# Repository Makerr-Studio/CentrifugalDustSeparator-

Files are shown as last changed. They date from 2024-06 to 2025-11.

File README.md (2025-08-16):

# CentrifugalDustSeparator
Centrifugal Dust Separator - MK2 - 3D Files for printing (Beta release)<br>
Support me on: https://www.patreon.com/CapturingDust

Tube suppliers may vary based on your geographic location, and so do the tube dimensions.<br>
Files are adjusted accordingly, see README files in the spesific build versions for suppliers info:<br>
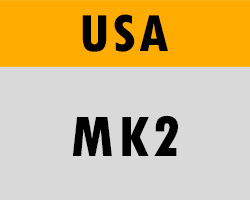
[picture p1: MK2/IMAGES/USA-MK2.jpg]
 
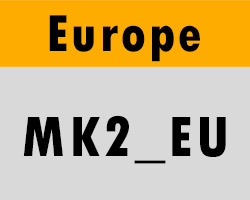
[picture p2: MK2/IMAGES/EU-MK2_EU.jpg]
 
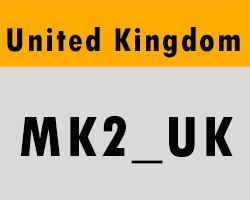
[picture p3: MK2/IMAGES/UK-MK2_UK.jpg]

<br>*note: First print the scaling ring to check your tube dimensions. See: https://www.youtube.com/shorts/JZXLTLeB2oE
<br>**note: For parts that are not listed in the subfolders (such as the Y-pieces) see the normal MK2 version.<br>

All parts are designed to print on bambulab build volume(WxDxH) 256 x 256 x 256 mm³.<br>
Only the Y-pieces are not compatable with the Prusa build plate.
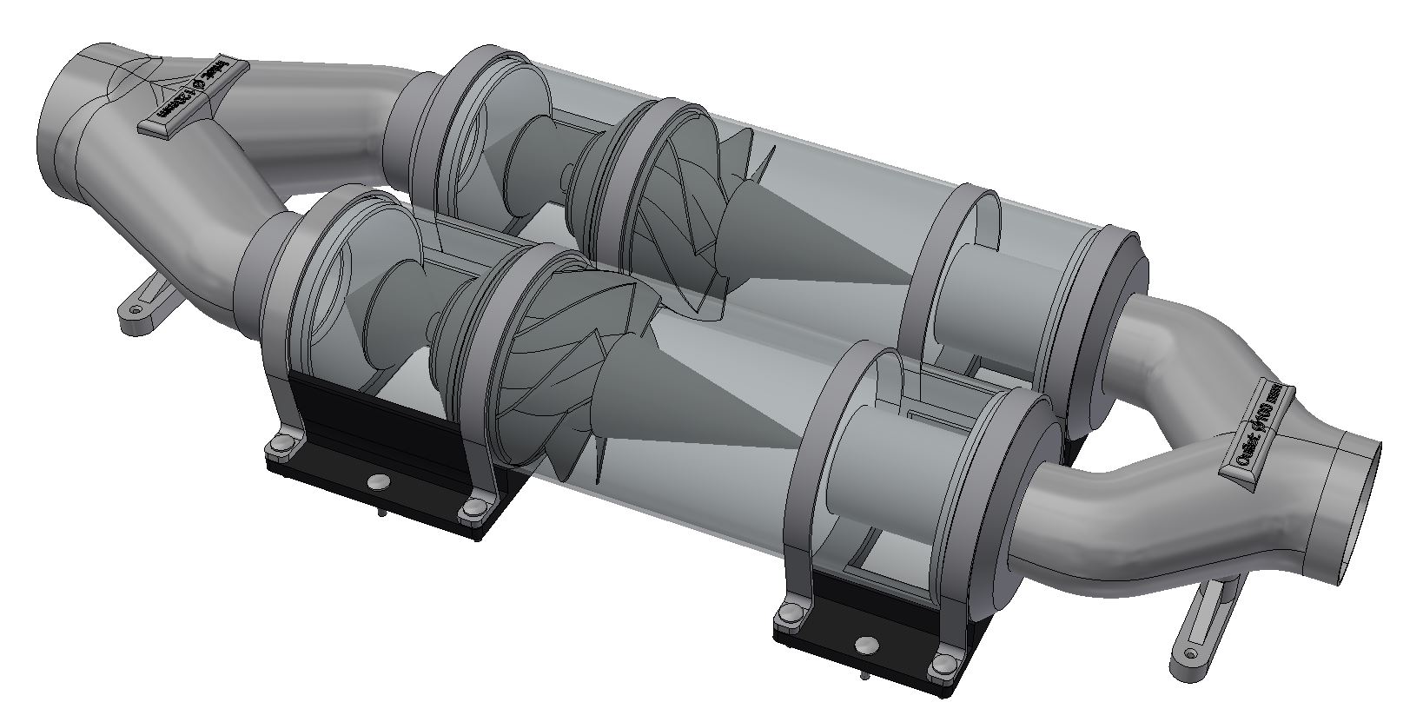
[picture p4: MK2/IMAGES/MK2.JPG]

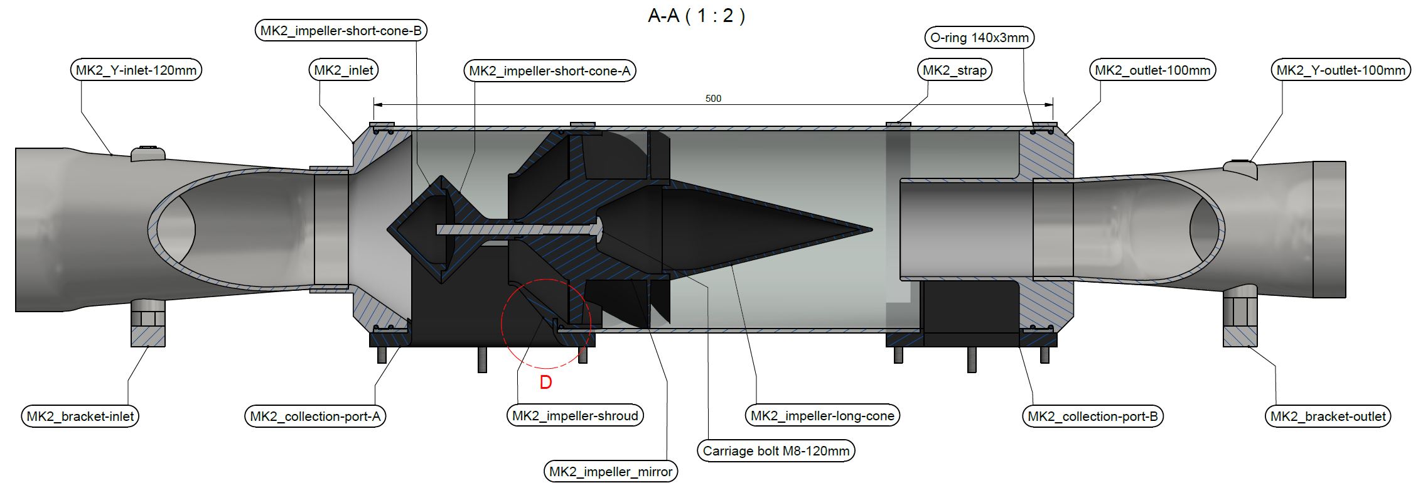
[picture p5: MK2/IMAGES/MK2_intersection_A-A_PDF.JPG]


<h2>YouTube: @CapturingDust</h2>
For the test video see:

https://www.youtube.com/watch?v=ENybYVAr11Q&t=1102s

Part 1 of the build video is available on Youtube: https://www.youtube.com/watch?v=bCNDPIjRccw

Part 2 of the build video is available on Youtube:
https://www.youtube.com/watch?v=j7K9fEa8Re8

<h2>Parts/Supplies:</h2>
The MK2 base version is designed for 6" Clear PVC  = https://www.amazon.com/dp/B09NJLNW58?psc=1&ref=ppx_yo2ov_dt_b_product_details

<br>EU alternative Acrylic tube 150x3mm (real size 151x3.5mm)= https://www.kunststofforte.nl/product/transparante-acrylaat-buizen-xt/<br>
UK alternative Acrylic tube 150x3mm (real size 150.05x3.1mm)= https://plasticonline.co.uk/150mm-diameter-clear-acrylic-tube.html

O-ring MK2     = https://www.kramp.com/shop-de/de/p/o-ring-140-x-3--OR1403P001
<br>O-Ring MK2_EU  = https://www.kramp.com/shop-de/de/p/o-ring-120-x-3--OR1203P001

Collection container        = Festool VAB-20/1 part nr. 204294 (204295 in my case because its a pack of 3).
<br>(For US: $79.60 set of 3 - Free shipping: https://www.hartvillehardware.com/product/sku-1337339/festool-dust-extractors-accessories)

Compresion tape: 50 mm x 30 m x 3mm version of this tape: https://bluedolphintapes.com/product/acoustic-tape/

3D printable Systainer T-Loc: https://www.printables.com/model/313989-systainer-t-loc

<h2>Original build</h2>
Inspired by Pilson Guitars build project<br>
Youtube: https://www.youtube.com/watch?v=R4R9GfCQrW4&<br>
Github: https://github.com/pilsonguitars/centrifugalDustSeparator

<h2>Changelog:</h2><br>
16-08-2025: 200mm single tube Centrifugal dust Separator STEP-files added. Including third stage integration. Used Acrylic tube 200x3mm from: https://www.kunststofforte.nl/product/transparante-acrylaat-buizen-xt/ 
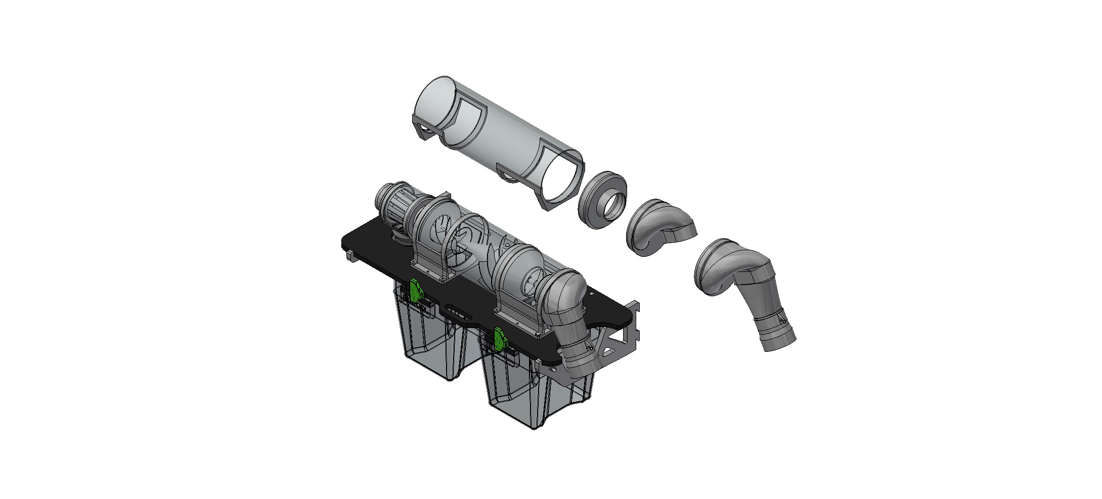
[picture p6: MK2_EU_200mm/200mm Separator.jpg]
<br>
15-01-2025: STEP-files of Y-piece, bracked and inlet added for 100mm tube to MK2 and MK2_EU. <br>
06-10-2024: Prusa printable Y-pieces added to folder <a target="_blank" rel="noopener noreferrer" href="MK2/STEP/">MK2/STEP</a><br>
29-09-2024: Changed the README file to better explain the differend design folder.<br>
28-09-2024: I did find out that a normal nut won't lock the impeller assembly for the long run. PLA will shrink/compress over time, and loosens the nut. Use a spring washer & lock nut instead!<br>
14-09-2024: Added the REV2 files of the Y-pieces + brackeds. They need less material to print now by removing the needs for support. Thx @philreindl for the tip!<br>
11-09-2024: In the folder <a target="_blank" rel="noopener noreferrer" href="MK2_EU/">MK2_EU</a> I added the Shaper files (.svg and also the .DXF's) and the Fusion archive files (.f3d) of the baseplate and cleat.<br>
08-09-2024: Parts for the French Cleats added. Fusion file is in the making. Type of compresion tape added.<br>
05-09-2024: Parts for the T-Loc added. Note: I did not print the latch and latch cover (these are just the 3D STEP files I used for the design, feel free to try to 3D print them)<br>
24-08-2024: MK2_EU Inlet and outlet parts adjusted for a better O-ring seal/fit for the 120x3mm O-rings.<br>
19-08-2024: Added 120x3mm O-rings i switced to while building the EU version. Still need to change the parts for a better fit. Will make testprints for this in the next weeks.<br>
10-08-2024: Added BAMBU LAB and OrcaSlicer files to MK2_UK.<br>
07-08-2024: <a target="_blank" rel="noopener noreferrer" href="MK2_UK/">MK2_UK</a> Step Files added for UK version Tube. Not printed of tested yet. <br>
07-08-2024: <a target="_blank" rel="noopener noreferrer" href="MK2_EU/">MK2_EU</a> files added for EU alternative. Not tested jet. <br>
02-08-2024: OrcaSlicer file from mirrored impeller added.<br>
01-08-2024: All .3fm files are available now. Also added all the .stl-files.<br>
29-07-2024: To solve issues with print imperfections on the mirrored impeller; Use the open-source OrcaSlicer and set the wall loop direction to clockwise. Thx @Mik3503 for the tip!
(*Go to the <a target="_blank" rel="noopener noreferrer" href="[MK2/STEP/](https://github.com/SoftFever/OrcaSlicer/releases)">GitHub</a> page, scroll down to the assets section and download the latest release compatible with your operating system, and then install it)<br>
21-07-2024: Folder BAMBU LAB added with the .3mf files for Bambu Lab. Added the impeller and impeller-mirror and fixed the Non-manifold edges error. (Working on the other .3fm files to add)

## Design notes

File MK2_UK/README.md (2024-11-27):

Files adjusted for UK tube: https://plasticonline.co.uk/150mm-diameter-clear-acrylic-tube.html
<br>Print the mirrored impeller with the OrcaSlicer file clockwise for clean print results.

I adjusted the MK2 files to the UK tube dimensions:

    Wall thickness: 3.1mm
    OD: 150.05mm
    ID: 144.16mm

*had to scale down MK2_UK_impeller-shroud.3mf (along with the impeller) to 99.9 as at 100% it was just too snug to push further down the tube past the opening. Check your tube dimensions always with the scaling ring.

Github member <a target="_blank" rel="noopener noreferrer" href="https://github.com/3dtrix">3dtrix</a> from Germany purchased his tubes from this online shop (Original Plexiglas manufacture):
<br>150mm / 3mm
<br>https://www.plexiglas-shop.com/de/produkte/ro0a070gt.html
<br>They ship to EU incl. UK<br><br>

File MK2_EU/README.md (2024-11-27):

Centrifugal Dust Separator - MK2_EU - 3D Files for printing (Beta release)<br>
Support me on: https://www.patreon.com/CapturingDust

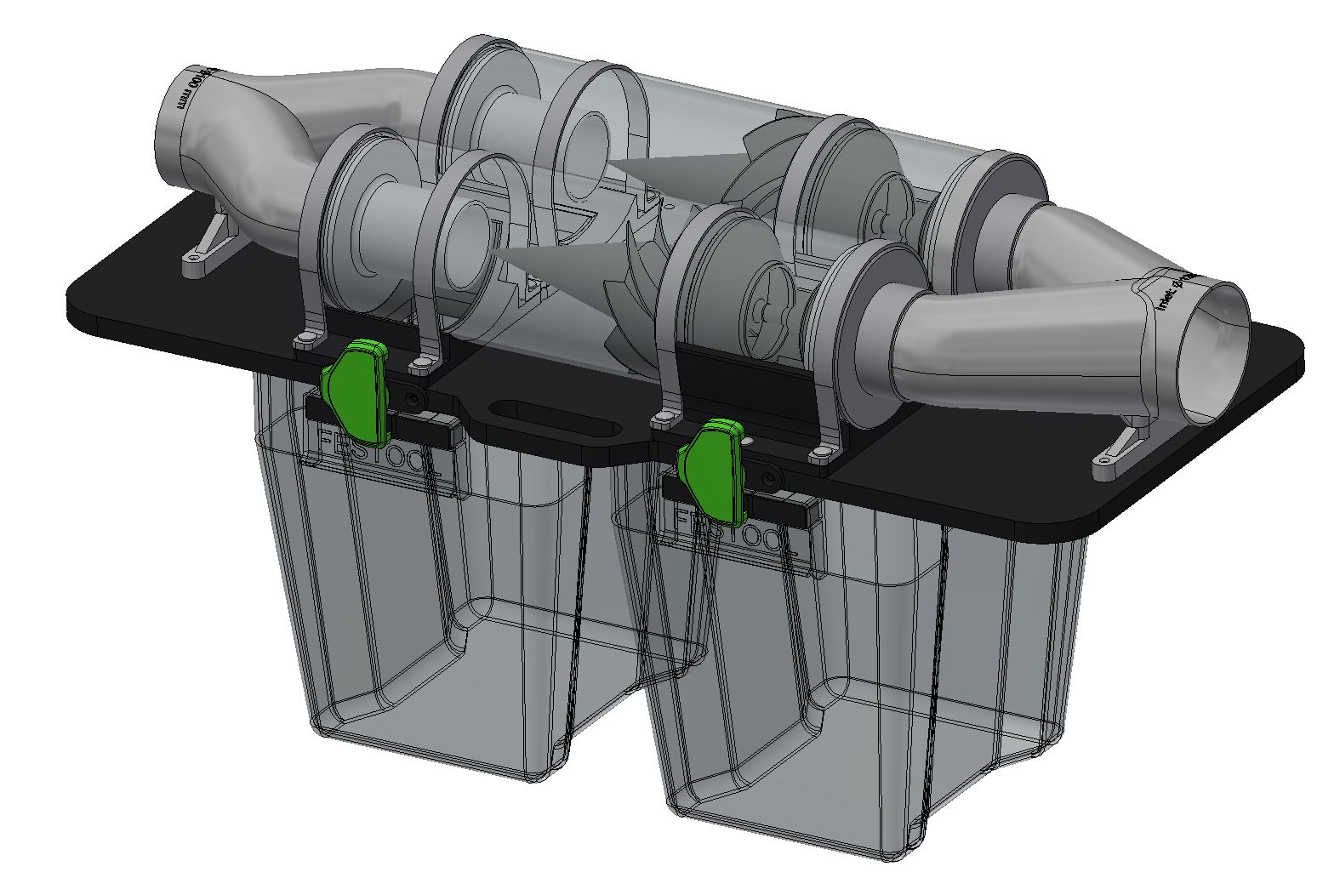
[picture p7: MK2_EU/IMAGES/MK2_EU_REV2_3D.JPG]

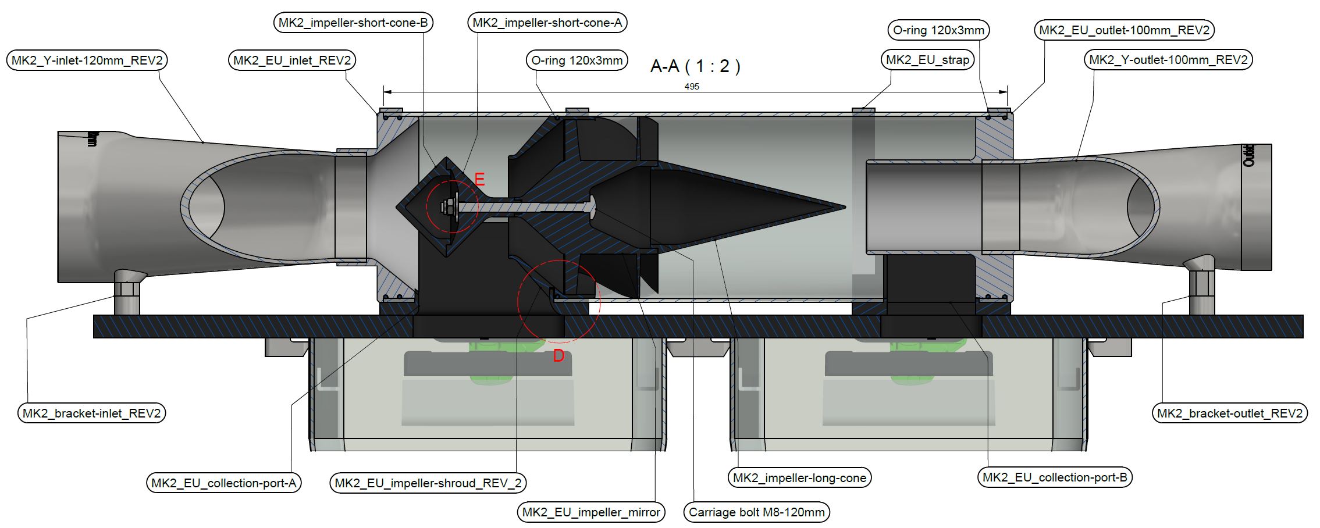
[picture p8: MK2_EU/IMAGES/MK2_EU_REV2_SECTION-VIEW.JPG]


Files adjusted for EU 150x3mm tube: https://www.kunststofforte.nl/product/transparante-acrylaat-buizen-xt/
Print the mirrored impeller with the OrcaSlicer file clockwise for clean print results.

120x3mm O-Ring EU = https://www.techniekwebshop.nl/o-ring-120-x-3-or1203p001-makkelijk-vervormbaar-precisie-o-ring-nitrilrubber-nbr-din-3771-70-amp-deg-sh-120-mm.html

I adjusted the MK2 files to the real life EU Kunststofforte tube dimensions I measured:

    Wall thickness: 3.5 mm
    OD: 151,375 mm
    ID: 144,375 mm

Patreon member purchased his tubes at a German seller on Amazon: https://www.amazon.com.be/dp/B0CBKV2Y2K
<br>    ID: 143,46 mm
<br>    EU Files printed at 99.4% scale (Check your tube dimensions always with the scaling ring.)

Github member <a target="_blank" rel="noopener noreferrer" href="https://github.com/3dtrix">3dtrix</a> from Germany purchased his tubes from this online shop (Original Plexiglas manufacture):
<br>150mm / 3mm
<br>https://www.plexiglas-shop.com/de/produkte/ro0a070gt.html
<br>They ship to EU incl. UK<br><br>

<h2>Latest versions</h2>
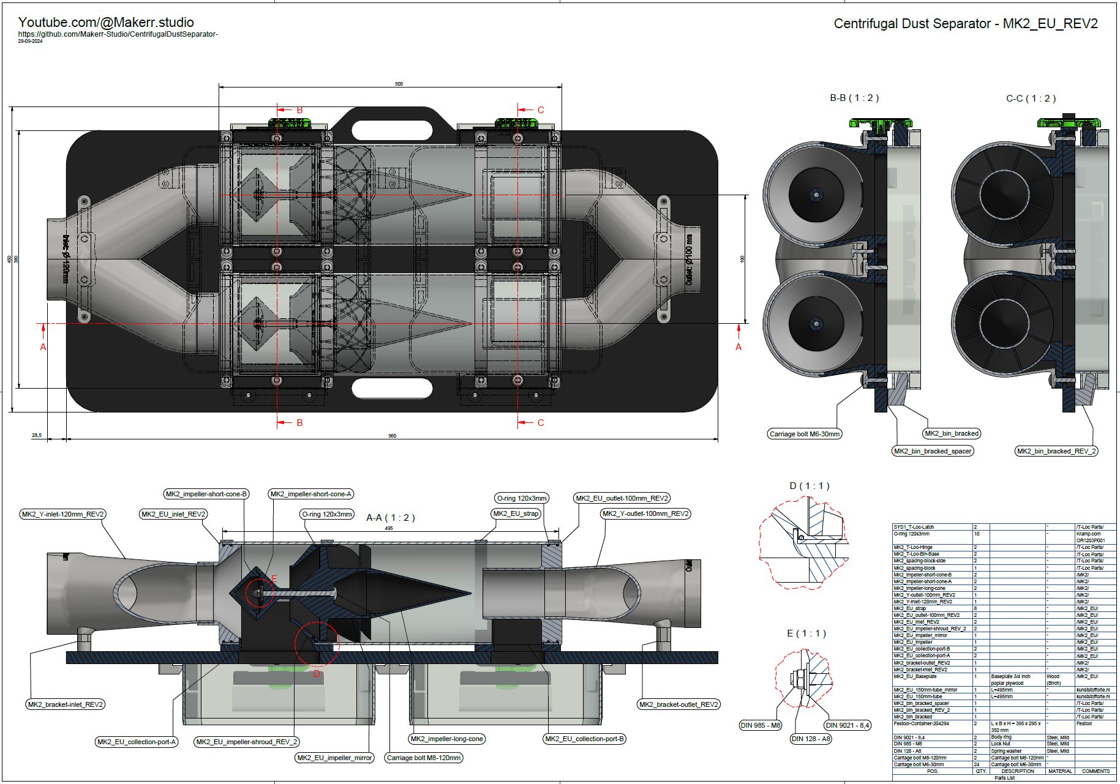
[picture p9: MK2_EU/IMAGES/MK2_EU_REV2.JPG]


<h2>Old versions</h2>
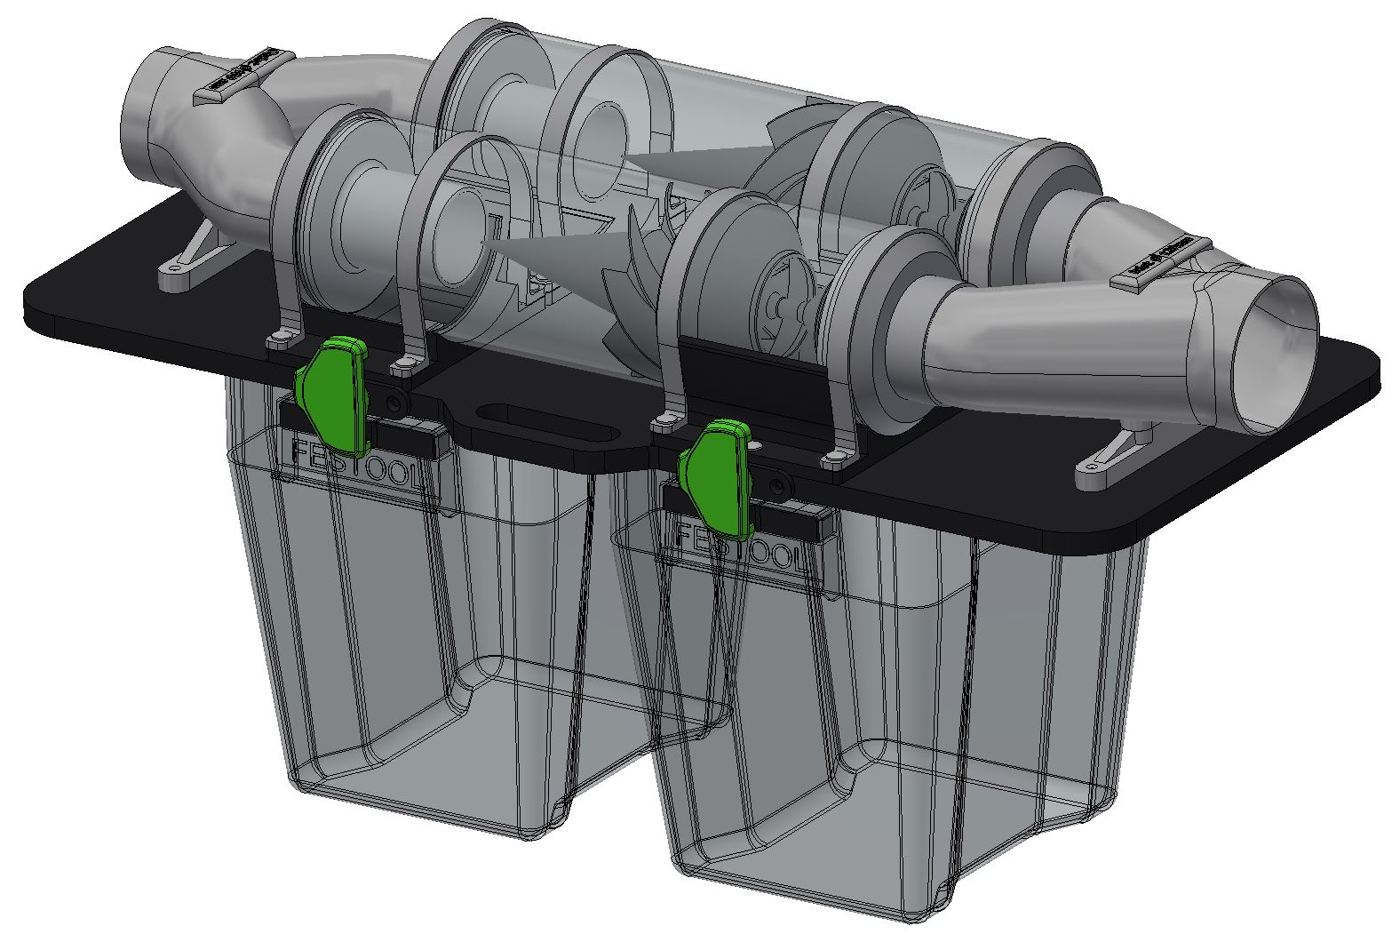
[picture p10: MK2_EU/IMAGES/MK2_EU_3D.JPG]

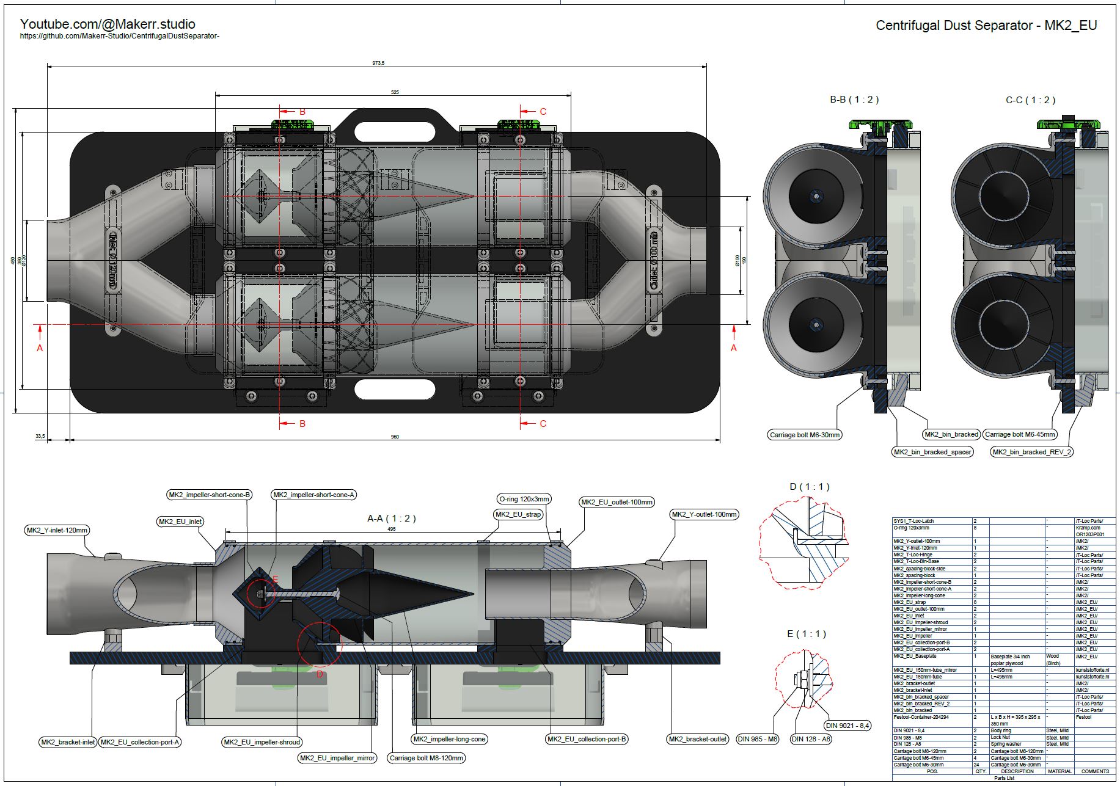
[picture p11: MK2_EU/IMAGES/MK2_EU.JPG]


<h2>Changelog:</h2><br>
29-09-2024: Completed the drawing files of MK2_EU_REV2. Added the STEP-files for the REV2 parts.<br>
24-08-2024: Inlet and outlet parts adjusted for a better O-ring seal/fit for the 120x3mm O-rings.<br>
19-08-2024: Added 120x3mm O-rings I switched to while building the EU version. Still need to change the parts for a better seal/fit. Will make testprints for this in the next week.

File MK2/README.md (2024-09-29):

The MK2 base version is designed for 6" Clear PVC  = https://www.amazon.com/dp/B09NJLNW58?psc=1&ref=ppx_yo2ov_dt_b_product_details<br>

Tube dimensions I measured:

    Wall thickness: 3,01 mm
    OD: 151,822 mm
    ID: 145,800 mm

Patreon member purchased his tubes at Woodcraft: 
<br>  https://www.woodcraft.com/products/woodriver-dust-connection-clear-pvc-tube-36-x-6 
<br>  Free Shipping with Code "PENCIL" $20 each
<br>Check your tube dimensions always with the scaling ring.

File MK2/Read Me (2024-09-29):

The MK2 base version is designed for 6" Clear PVC  = https://www.amazon.com/dp/B09NJLNW58?psc=1&ref=ppx_yo2ov_dt_b_product_details<br>

Tube dimensions I measured:

    Wall thickness: 3,01 mm
    OD: 151,822 mm
    ID: 145,800 mm

Patreon member purchased his tubes at Woodcraft: 
  https://www.woodcraft.com/products/woodriver-dust-connection-clear-pvc-tube-36-x-6 
  Free Shipping with Code "PENCIL" $20 each
  MK2 Files printed at 99.6% scale

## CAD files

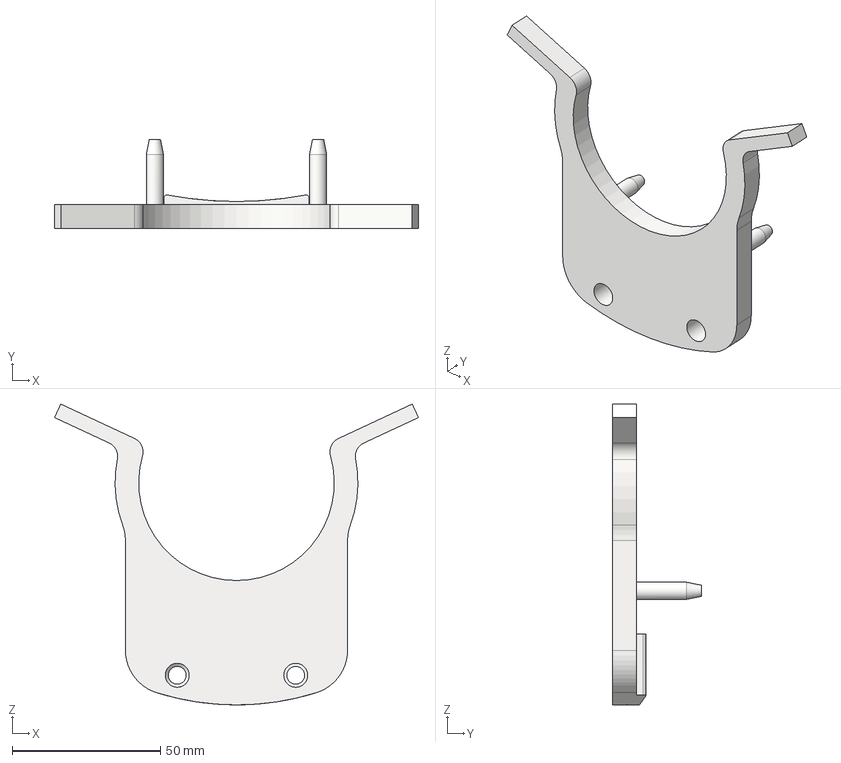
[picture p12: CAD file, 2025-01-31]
BT-100 Anemometer Jig/BT-100-JIG_Base.stp
122.9 x 30.0 x 101.6 mm

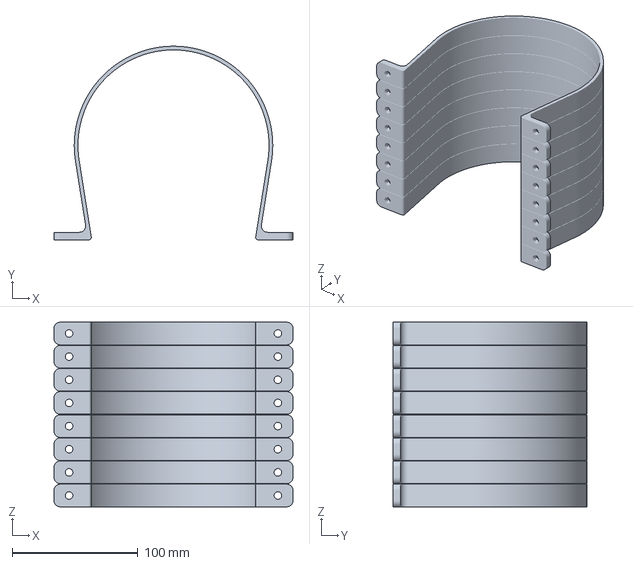
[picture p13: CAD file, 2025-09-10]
MK2/BAMBU LAB/MK2_strap_stacked.3mf
190.0 x 153.9 x 146.8 mm

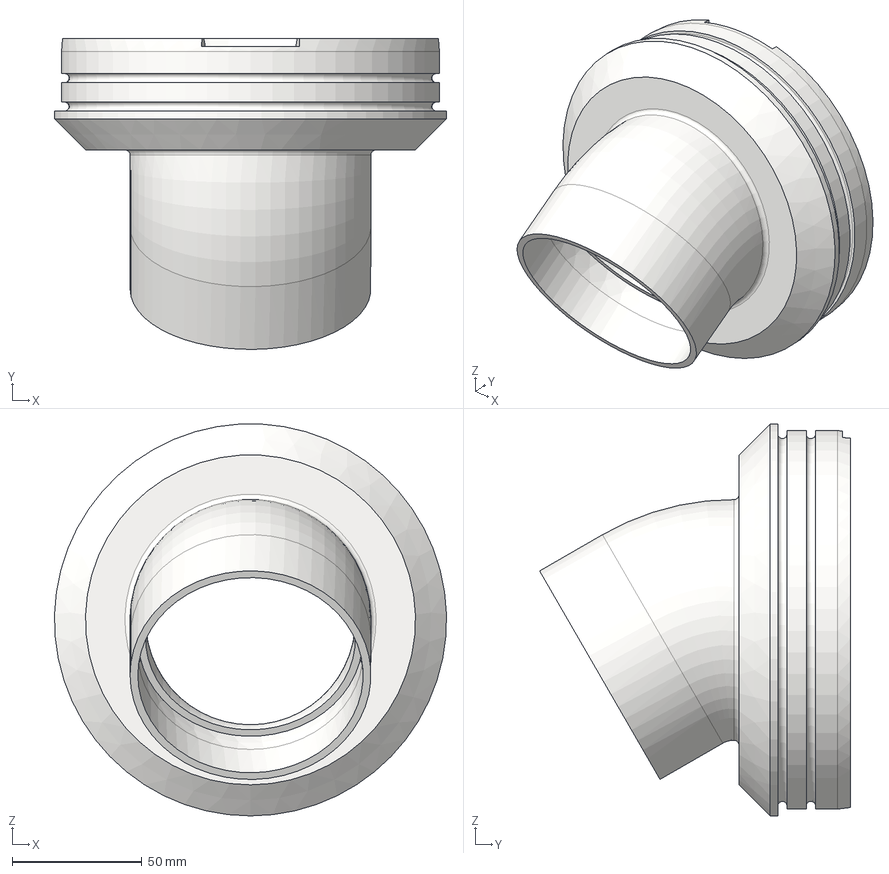
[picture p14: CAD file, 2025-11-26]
MK2/NOT TESTED - REQUESTED PARTS/MK2_inlet-30-degrees.stp
151.4 x 120.0 x 151.3 mm

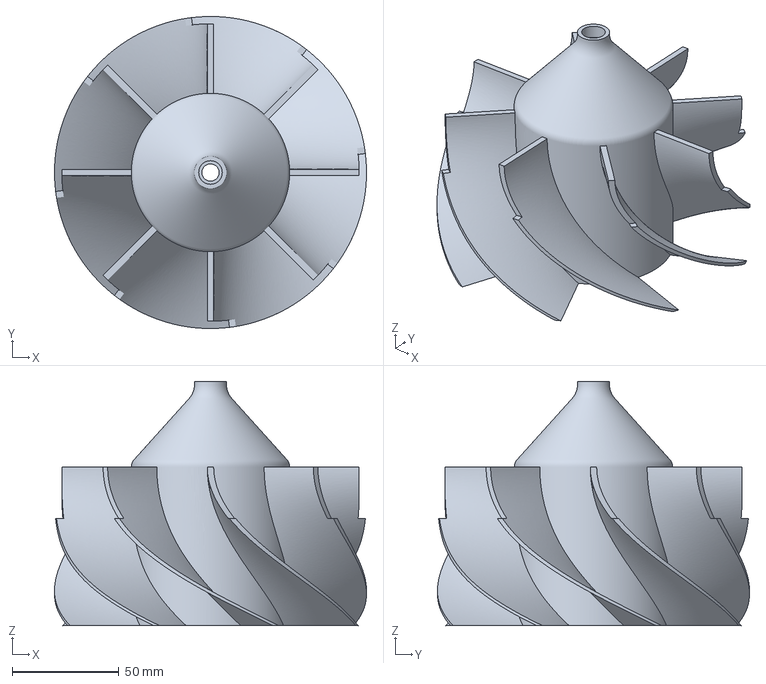
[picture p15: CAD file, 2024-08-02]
MK2/OrcaSlicer/MK2_impeller_mirror.3mf
145.8 x 145.8 x 114.2 mm

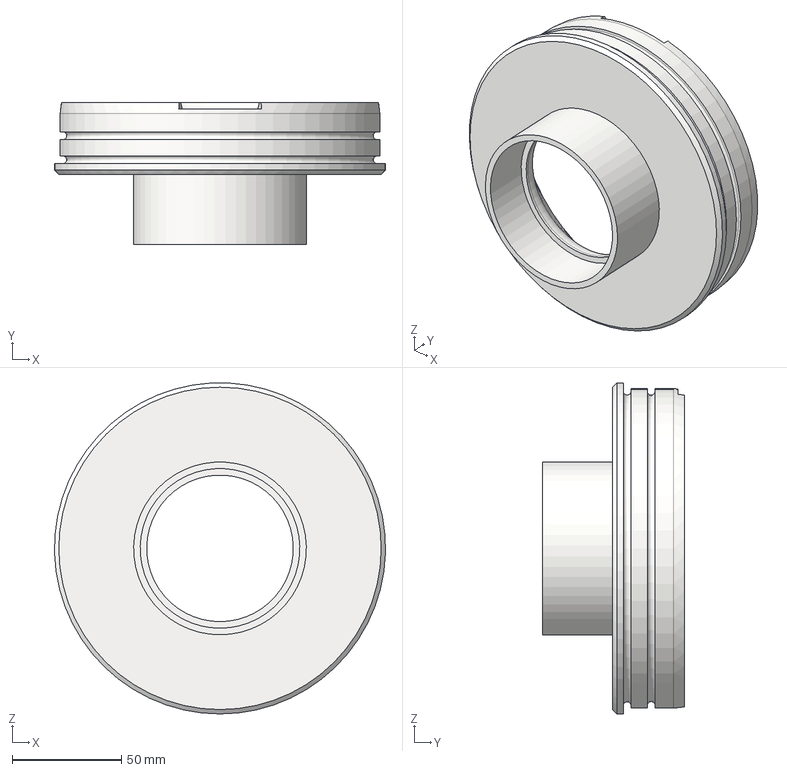
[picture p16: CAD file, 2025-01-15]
MK2/STEP/MK2_inlet_100mm_REV2.stp
151.4 x 65.0 x 151.3 mm

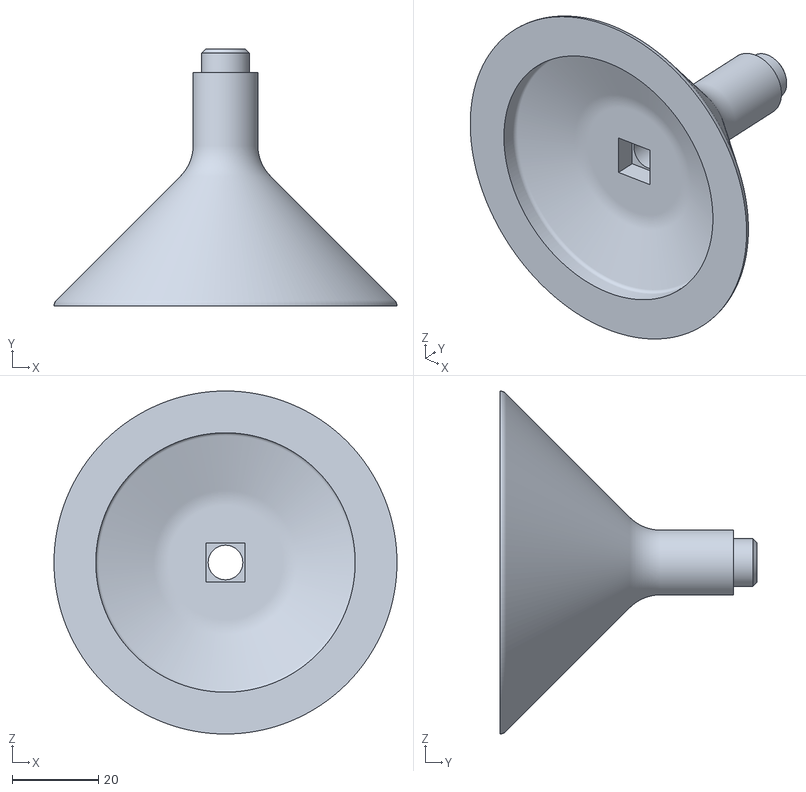
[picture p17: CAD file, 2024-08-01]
MK2/STL/MK2_impeller-short-cone-A.stl
79.3 x 59.5 x 79.3

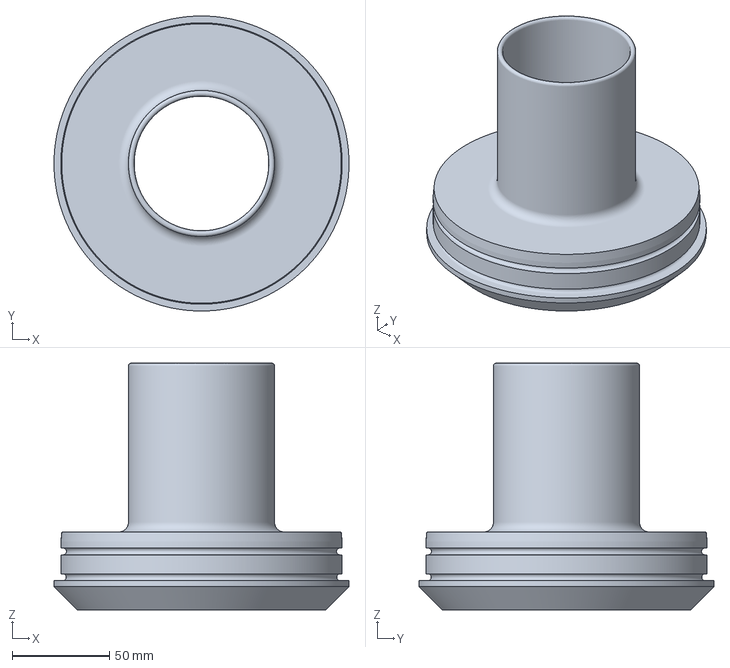
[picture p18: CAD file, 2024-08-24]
MK2_EU/BAMBU LAB/MK2_EU_outlet-100mm.3mf
151.4 x 151.4 x 126.6 mm

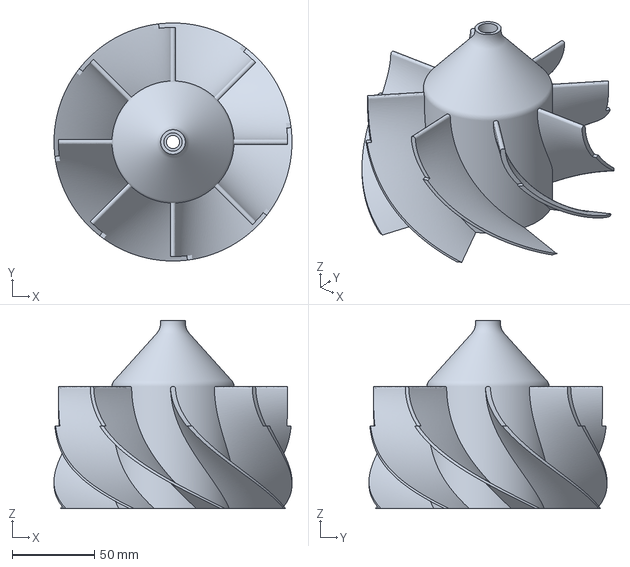
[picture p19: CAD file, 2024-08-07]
MK2_EU/OrcaSlicer/MK2_EU_impeller_mirror.3mf
144.4 x 144.4 x 114.2 mm

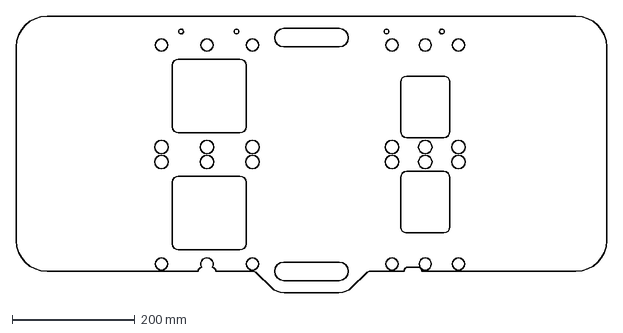
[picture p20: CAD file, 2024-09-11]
MK2_EU/Shaper/MK2_EU_baseplate.dxf
960.0 x 450.0 mm

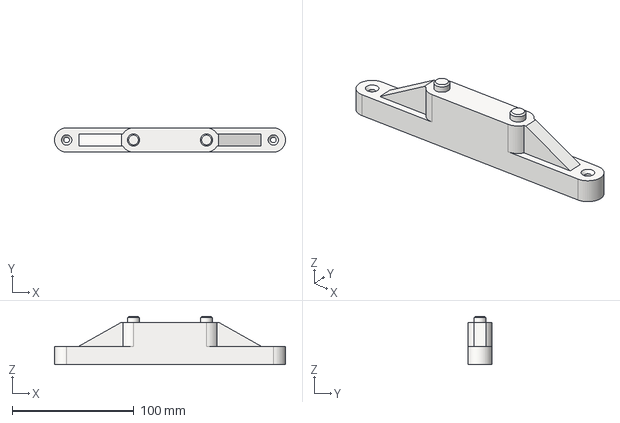
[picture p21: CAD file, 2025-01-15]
MK2_EU/STEP/MK2_EU_bracket-inlet-100mm.stp
190.0 x 20.0 x 39.5 mm

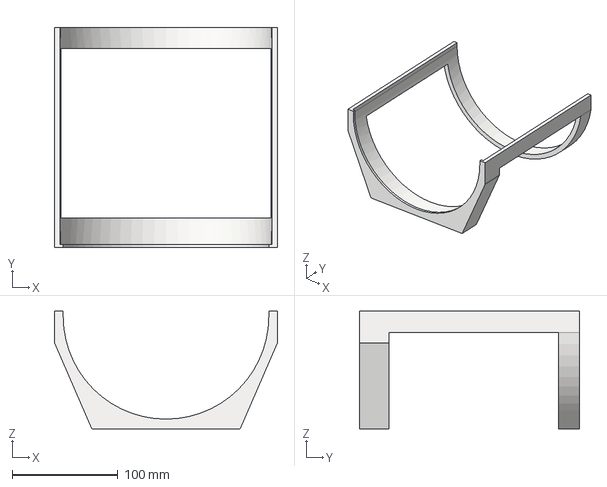
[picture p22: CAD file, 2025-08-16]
MK2_EU_200mm/MK2_EU_8inch_A-cutting-jig.stp
210.6 x 208.0 x 111.4 mm

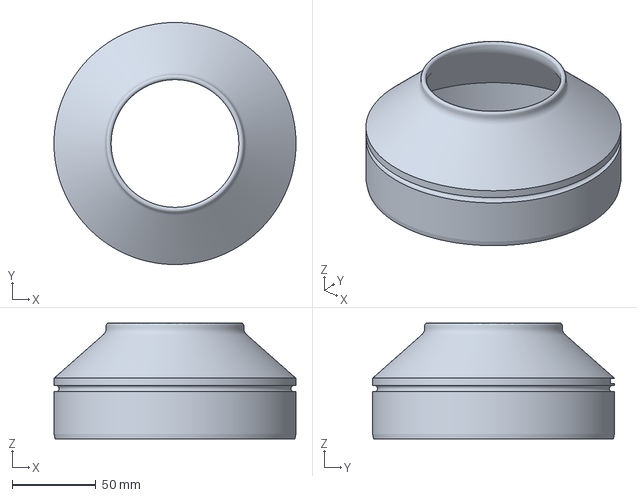
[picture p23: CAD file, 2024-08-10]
MK2_UK/BAMBU LAB/MK2_UK_impeller-shroud-o-ring.3mf
144.2 x 144.2 x 69.0 mm

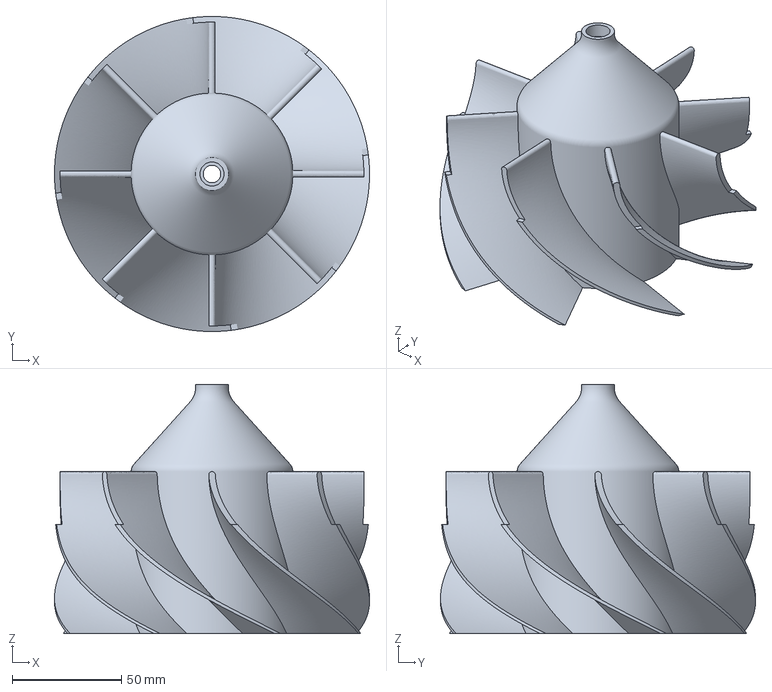
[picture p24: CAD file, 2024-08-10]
MK2_UK/OrcaSlicer/MK2_UK_impeller_mirror.3mf
144.1 x 144.1 x 114.2 mm

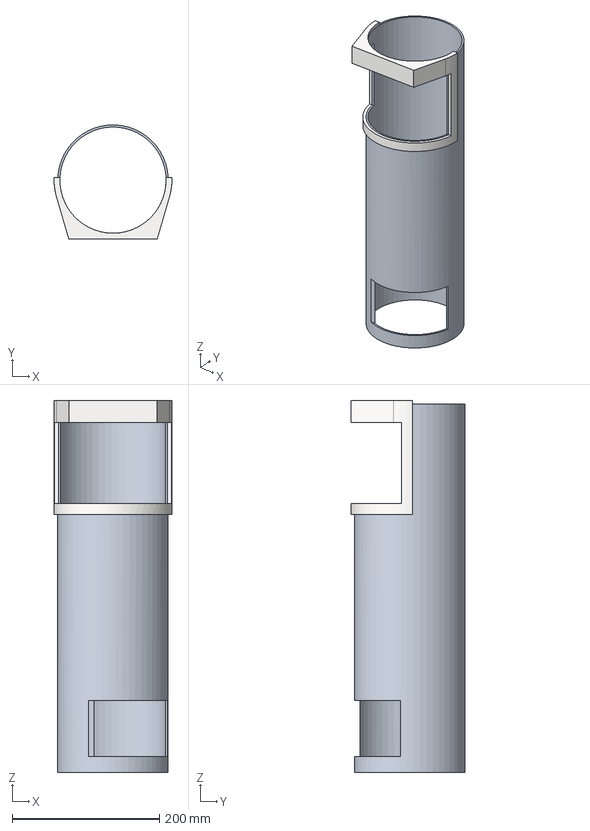
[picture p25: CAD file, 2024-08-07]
MK2_UK/STEP/MK2_UK_port-A-cutting-jig.stp
159.9 x 155.0 x 505.0 mm

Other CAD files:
T-Loc Parts/Festool-Container-204294.stp
BT-100 Anemometer Jig/BT-100-JIG_insert_100mm.stp
MK2/BAMBU LAB/MK2_bracket-outlet_REV2.3mf
MK2/NOT TESTED - REQUESTED PARTS/MK2_inlet-45-degrees.stp
BT-100 Anemometer Jig/BT-100-JIG.3mf
BT-100 Anemometer Jig/BT-100-JIG_insert_120mm.stp
MK2/BAMBU LAB/MK2_Y-outlet-100mm_REV2.3mf
MK2/BAMBU LAB/MK2_bracket-inlet.3mf
MK2/BAMBU LAB/MK2_bracket-inlet_REV2.3mf
MK2/BAMBU LAB/MK2_bracket-outlet.3mf
MK2/BAMBU LAB/MK2_collection-port-A.3mf
MK2/BAMBU LAB/MK2_collection-port-B.3mf
MK2/BAMBU LAB/MK2_impeller-mirror.3mf
MK2/BAMBU LAB/MK2_impeller-short-cone-A.3mf
MK2/BAMBU LAB/MK2_impeller-short-cone-B.3mf
MK2/BAMBU LAB/MK2_impeller-shroud.3mf
MK2/BAMBU LAB/MK2_impeller.3mf
MK2/BAMBU LAB/MK2_inlet.3mf
MK2/BAMBU LAB/MK2_outlet-100mm.3mf
MK2/BAMBU LAB/MK2_port-A-cutting-jig.3mf
MK2/BAMBU LAB/MK2_port-B-cutting-jig-mirror.3mf
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

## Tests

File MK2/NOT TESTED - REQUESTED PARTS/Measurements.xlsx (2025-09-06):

 | % | KG/h
A | 99.57 | 33.3214
A | 99.83 | 93.945
A | 99.86 | 100.975
A | 99.85 | 139.764
A | 99.77 | 253.573
A | 98.85 | 281.02
A | 98.23 | 554.191
A | 92.78 | 925.764
B | 99.76 | 27.3361
B | 99.81 | 68.119
B | 99.71 | 85.5803
B | 99.89 | 184.74
B | 99.89 | 251.373
B | 99.72 | 306.706
B | 94.26 | 552.366
B | 97.05 | 794.242
B | 81.02 | 1115.23
C | 99.24 | 168.131
C | 99.92 | 35.6882
C | 99.86 | 133.586
C | 61.6 | 692.051
C | 99.98 | 23.9899
D | 99.79 | 220.614
D | 99.89 | 35.9712
D | 99.72 | 308.498
D | 99.46 | 968.498
D | 94.12 | 1686.28

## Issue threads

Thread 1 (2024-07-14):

Question/Suggestion: Option for 3d-printed tube using transparent materials?

zihotki, 2024-07-14:
Hey, I LOVE the separator and wanted to build one too. I found that for me the transparent tubes are hard to find and they are quite expensive. Since I had success with using transparent materials for some purposes where you don't need to see many details. I wonder if you considered replacing the tube by a printed one. Using a printed one it may be easier to design the tube to have mounting points built in. A spool or two of a generic transparent filament are  much cheaper too.

I wasn't sure what was the best way to share the idea so I followed my programmer's habit via github.

Makerr-Studio, 2024-07-15:
Hi Vasili Puchko!

Thank you for responding!

Your idea of printing the tube in a generic transparent filament i considered myself for a moment in the beginning. I did not liked the extreme shipping cost of the PVC tube to send it to the EU. But for me it was the easiest way forward and i have no experiance with printing vlear filaments.

I am testing a EU alternative Acrylic tube 150x3mm = https://www.kunststofforte.nl/product/transparante-acrylaat-buizen-xt/

Mayby in the future i will design a complete printed version. For now i am focusing on the performance part to squeeze the maximum out of it.

zihotki, 2024-07-16:
@Makerr-Studio I think we can collaborate a bit on the separator. At the moment I'm working on DIY version of vacuum similar to Record Power CGV286-4 based on idea of Ingos Tips https://www.youtube.com/watch?v=2-J8GXajv78 but with 3d-printed motor housing. So far the total price of all components is about 170 euro including filament. And for that I'm also building a Thien's cyclone separator ( https://www.jpthien.com/cy.htm ) since it's a simpler version compared to one you're working.

I'm also planning to build the version you're working and It would be great to compare the performance of the solutions. And I can play around with the printed version of the tube as well.

Makerr-Studio, 2024-07-16:
Please tell me, can you read my mind.. (Or we draw inspiration from the same videos :D ).

I have a ultimate goal in my head to end with a modular system out of Festool/Tanos SYS3 XXL Systainer. One for the 2 camvac motors, frequency controlled + filters (Only i am not a electrical engineer :D). And one for the separator. A bit like a mix-and-match system that can be adjusted according to the situation. I asked myself the question: What if Festool designed a portable dust extractor with a hi-volume? How would it be like?

Tree days ago i ordered a simple 120L trashcan to make a $2 dust separator for it (Level 1). I also will make a Thien Baffle cyclone as a Level 2 separator. I also ordered a Oneida-Air Super Dust Deputy 4/5 cyclone a month ago, (only in Holland it has a delivery time of 2-4 month) so still waiting on that to be delivered. I am very curious about how they perform in relation to each other.

My coal for the channel is to develop a test-rig/test protocol that is accurate and repeatable to compare the different Levels of dust separators (and optimize mine even more). I will also measure airflow, pressure loss and count the partiles from 0,3 μm, 0,5 μm, 1,0 μm, 2,5 μm, 5,0 μm, 10,0 μm with a particle counter. Still figuring out the best setup for it and a way to automatically feed the material, i do have some ideas already.

No one on Youtube does that. And measuring the particle size that is not filtered out is the most important thing for a good dust filter i think.

So feel free to contribute! Do you also have a youtube channel or something?

asucks, 2024-07-19:
> I have a ultimate goal in my head to end with a modular system out of Festool/Tanos SYS3 XXL Systainer. One for the 2 camvac motors, frequency controlled + filters (Only i am not a electrical engineer :D). And one for the separator. A bit like a mix-and-match system that can be adjusted according to the situation. I asked myself the question: What if Festool designed a portable dust extractor with a hi-volume? How would it be like?

Awesome.   Been working with stuff that creates super fine dust for 20 years now and have never found a perfect solution in a dust collector.  I started researching again recently and came to the same conclusion that you did, that it has to be some sort of hybrid system that combines high flow and high pressure (I've always had high flow and CFM, not enough pressure because of restriction).

A couple months ago, I stumbled upon @pilsonguitars centrifugal dust separator videos, but it still seemed too advanced and technical for me.  But it did seem very promising when I had more time to research and learn.  I started researching again a week ago and found your video, and realized we had a lot of similar goals, skills, and equipment.

Both you guys are way smarter than me, but I do own a small manufacturing firm, I have a 3D printer, and I am willing to make an exact copy of what you are so we can make sure your testing results are accurate.  I've already got the majority of the parts 3D printed, just waiting on the tubing, which will be here in a few days.

> My coal for the channel is to develop a test-rig/test protocol that is accurate and repeatable to compare the different Levels of dust separators (and optimize mine even more). I will also measure airflow, pressure loss and count the partiles from 0,3 μm, 0,5 μm, 1,0 μm, 2,5 μm, 5,0 μm, 10,0 μm with a particle counter. Still figuring out the best setup for it and a way to automatically feed the material, i do have some ideas already.

Perfect.  I'm totally willing to get the same testing equipment and develop measurement standards so we can verify the data.  I don't have a YouTube channel or have the time to run one, but I can film any test equipment you need me to and transfer it over for you to use.  My main goal is to get the small stuff too, for the health and safety of my employees and myself, so getting the right equipment and making sure it was really capturing it would be a bonus for me.

I also have some additional ideas that I think will get it to 100% capture rate with an additional stage.  Any way we can setup a zoom call so we can bounce some ideas around, I can show you my setup, and you can verify some things for me as I continue my build?

Makerr-Studio, 2024-07-19:
@asucks Awesome you stumbled upon oure centrifugal dust separator video's! Nice to hear you are printing one yourself. I found out thad the right tolerances are critical. So thats wy i add the scaling ring to the files to make it fit perfectly!

Back to the design. At first glance I also thought the centrifugal dust separator looked very complex. The design really fascinated me because it looked cool and technically challenging and it is compact in height, which is exactly what I needed for my small space.

Not much research has been done into these types of separators. And the Harvey system is very expencive with mixed feedback from end users. Some say it's marketing only and it doesn't work. Others are very enthusiastic about it (not clear what is PR). I would like to quantify that, and compare it with other type of separators. To see what works best for a certain type of dust mixtures.

I realy like to hear more about you usecase! Only my English is very rusty at the moment. So a zoom call is a bit challaging for me to speek it live. On camera i can record many takes :P. I work one day a week on the project. Still having a fulltime job. So time management is key for me on the project. Maybe you can record a short movie from your situation and send it to: maakhet@makerr.nl

schmidtw, 2024-09-02:
Has anyone tried printing a clear tube yet?  I am just getting into 3d printing & ordered some clear PETG to try printing a clear tube.  I'm not sure it will be clear enough for what we want based on the research, but the proof is found by doing.

The other ideas I have regarding the tubes:
- Instead of using one long tube per separator we could attempt to use several shorter tubes & print connectors so the tubes fit into connectors (that can also hold the turbines/etc where we want them)
- Resin cast shorter segments of tubing & bolt them together (this seems like a lot of work)
- Try using cardboard concrete tubes if we don't need to see the dust moving around.  At least in the US a 2m long tube is $10USD if you can get it locally.
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

Makerr-Studio, 2024-09-22:
No I have not tried printing a clear tube yet. Looks like the more layer thickness for the part the less clear it will be. It is somewhere on my list to try in the future. Did you try it already?

I also though about the idea to make it more modular..  with quick connect fittings so you are able to put together the best modules of the separator for the tool you need it for. That is quick connect I don't figured out yet. To get a realy good seal is a bit hard I think.

Cardboard can be a option, only I like to pay more to see the dust flow. Also for filming it is better to have a clear tube.

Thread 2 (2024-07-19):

125mm inlet/outlet

phillipsnick, 2024-07-19:
Hey, thanks for your work on this! My printer is busy printing all the internal parts and tube/o rings have been shipped.

I've tried to make the changes in Fusion 360 but it's way above my skill level. Are there any plans in the future for Y splitters with 125mm inlet/outlet?

asucks, 2024-07-19:
hey Phil,

Others can chime in, but I would hold off on changing the sizes on anything for now.  I have a much larger inlet for my dust collector as well, but what I've learned over the years is bigger is not always better.

Your dust extractor might have a 125mm inlet, but it might not be able to maintain the pressure/speeds required to have the centrifuge run efficiently at 125mm, as it could be magnitudes difference in the volume of air.

That's why @Makerr-Studio is talking about his dream system being some sort of hybrid, one that can handle a high volume of air (high CFM with big inlets), but also one that maintains high speeds and pressure like those with smaller inlets.

Check out this video, this dude (and his marbles) can explain it better than I can:

https://www.youtube.com/watch?v=0NmMoIYIsr8

Makerr-Studio, 2024-07-20:
Hey Phil,

I have the CAD-files available on my computer! I will add those to the files soon. I tested my collector over 100mm tubing. I put the 100mm hose inside the 125mm Y-splitter. So I do not have good test results on that.

I need to order the tubing for that. Now I reduce at the planer from 125mm to 100mm. My goal is a 125mm inlet system attached to the 100mm camvac. Maybe the separation of the dust is enough to compensate for the volume change. Still need to test that.

Makerr-Studio, 2024-07-20:
I added the files to the following folder: MK2/NOT TESTED - REQUESTED PARTS

phillipsnick, 2024-07-24:
hey @asucks

Really ELI5 video that, thanks for sharing!

I'm still learning a lot about all this, but given than a smaller duct means more friction, wouldn't it make sense to keep things consistent from the fan where possible?
My extractor is rated at 2HP with a flowrate of 2000m3/hour (1177 CFM). So does have some power behind it!

phillipsnick, 2024-07-24:
@Makerr-Studio thanks for putting them together, will get printing over the next week.

If I have some left over filament I'll try print the originals too and do a side by side comparison and share some results if I have time!

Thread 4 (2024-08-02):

Y-Inlet requires supports

philreindl, 2024-08-02:
The Y inlet and Y outlet parts have bosses on them which require supports.  If the top boss was removed and the lettering embossed directly on the wall of the Y that would cut the supports in half.  If the bracket interface boss were to have a chamfer around the outside that would greatly reduce the supports needed there as well.

Thank you for this amazing work!

Makerr-Studio, 2024-08-02:
I see ware you going! It will reduce about 3 hours off printing time on the Inlet alone when we are able to print without supports.

When I have some time I will try to find a way to eliminate all the supports by using chamfers, or relocate the bracket interface.

Makerr-Studio, 2024-09-14:
@philreindl I just added the REV2 files of the Y-pieces + brackeds. They need less material to print now by removing the needs for support thanks to your tip!

Closed 2024-09-14.

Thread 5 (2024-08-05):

150x3mm UK Alternative

phillipsnick, 2024-08-05:
Just received 2x 500mm lengths of this https://plasticonline.co.uk/150mm-diameter-clear-acrylic-tube.html here in the UK.

Some quick tests with my callipers

- Wall thickness: 3.1mm
- OD: 150.05mm
- ID: 144.16mm

Noticed you have plans to release EU versions of the files in the future. If you need help with any test prints against these sizes let me know.

I was going to scale the original models, but if you have plans for specific versions it probably makes sense to wait!

Makerr-Studio, 2024-08-07:
Hi phillipsnick,

I received these tubes: https://www.kunststofforte.nl/product/transparante-acrylaat-buizen-xt/ here in the Netherlands.

I already adjusted the files to my dimensions:
- Wall thickness: 3.5 mm
- OD: 151,375 mm
- ID: 144,375 mm

The files are already printed. I just need to assemble all the parts and film the process. I will share the files with you, so you can check you are able to scale them to fit your tube. If not, I can adjust the parts for a UK version :D.

Makerr-Studio, 2024-08-07:
Hi phillipsnick,

I adjusted my files to your measurements. See the Step files:
https://github.com/Makerr-Studio/CentrifugalDustSeparator-/tree/main/MK2_UK"

Y-peaces are the same as MK2.

You need to check if the parts / O-rings will fit. I can adjust the files with your feedback if necessary.

phillipsnick, 2024-08-07:
Amazing @Makerr-Studio appreciate it!

I'll do some test prints at some point in the next week and report back :) Looking forward to seeing this thing in action

phillipsnick, 2024-08-09:
Managed to squeeze a few prints in to test this.

Scale ring fits snug at the 0 marker. 👍

Printed a few other parts to check fits

- Inlet/outlet port fit snug
- Y inlet/outlet (125mm version) fit perfectly

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

Noticed a couple of issues:

- [ ] [MK2_UK_impeller-shroud.stp](https://github.com/Makerr-Studio/CentrifugalDustSeparator-/blob/main/MK2_UK/STEP/MK2_UK_impeller-shroud.stp) is missing a o ring cut out?
- [] [MK2_UK_port-A-cutting-jig.stp](https://github.com/Makerr-Studio/CentrifugalDustSeparator-/blob/main/MK2_UK/STEP/MK2_UK_port-A-cutting-jig.stp) and [MK2_UK_port-B-cutting-jig.stp](https://github.com/Makerr-Studio/CentrifugalDustSeparator-/blob/main/MK2_UK/STEP/MK2_UK_port-B-cutting-jig.stp) haven't exported properly (see screenshot below)

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

Makerr-Studio, 2024-08-10:
Great to see the first parts fit perfectly!

I had removed the O-ring from the Impeller Shroud in the EU design I am building right now. I don't think the added value of the o-ring is really there if the shroud fits perfectly snug. And I have noticed that this also makes assembly a lot easier without.

Because you also use Bambu Lab slicer I just add two new folders to the MK2_UK folder.
- One with all the Bambu Lab files with the settings I did use myself, adjusted for the UK version. Also add a file for the Impeller Shroud with O-ring cut out.
- And one for the OrcaSlicer file for better print results of the mirrored impeller. Just in case you like to replicate the mirrored look. Printing two times the normal impeller setup works fine as well.

I did not had problems importing the cutting jigs into my slicer. Used the same STEP-files for that.

Please let me know if you need something else.

phillipsnick, 2024-08-16:
Makes sense regarding the O-ring, also can imagine it makes it a little bit more difficult to insert the part inside the tube.

Thanks for those files, they worked great. Not sure why when I was importing into OrcaSlicer they were coming out like that.

I had to scale down [MK2_UK_impeller-shroud.3mf](https://github.com/Makerr-Studio/CentrifugalDustSeparator-/blob/main/MK2_UK/BAMBU%20LAB/MK2_UK_impeller-shroud.3mf) (along with the impeller) to 99.9 as at 100% it was just too snug to push further down the tube past the opening. Which might be worth a note in the README?

Huge thanks for all your work on this 😁 you should add a donate link for some coffee/beer/PLA money.

I've printed all the parts, just need to figure out the cuts on the tubes and get it all bolted down!

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

Makerr-Studio, 2024-08-17:
Hi Nick!

Great to see it worked for you! I added files for the cutting jigs you can print and use as a cutting guide. Please be careful with the acrylic tube! It is in no way flexible as the PVC tube.

Don’t ask how I know 😅.

I used a oscillating multi tool to cut the acrylic. Use a blade with big teeth. Acrylic like to melt if not properly removed. I used a hardwood blade.
And protect yourself against toksick fumes of the acrylic and the hot chips.

Did your O-rings fit? I am building my EU design for video. Only had to order new smaller O-ring 120x3mm because the 140x3 are way to big in diameter and was a nightmare to fit inside the tube. Needed to reprint the in and outlets for that. You managed the fit as far I can see on your photo.

Please donate Tim from Philson Guitar! Without his work I would have been able to make mine version. Chears!

Closed 2024-08-16.

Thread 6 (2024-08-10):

Collection containers

RebelDesigner, 2024-08-10:
I love this design and I am getting ready to print it soon.
I do have a question about the collection containers from Festool. They are pretty expensive for just being plastic containers.
Did you think about other options?
For instance using cheaper clear plastic containers?
Wondering about an easy mechanisme to change the cheap storage bins and how they would seal.

PS: hoping for a new video soon! Please share more! Also interested is measurements about airflow reduction etc. (I will need a bigger motor I guess)

phillipsnick, 2024-08-10:
I’m in a similar boat, not a Festool user myself either so looking at other options.

I use IKEA storage boxes (https://www.ikea.com/gb/en/p/samla-box-with-lid-transparent-s99440774/) for a bunch of other hoarding. They are fairly sturdy and have a bit of strength to them.

Been sketching some ideas out for a plywood frame which applies just enough pressure on top of the box. Possibly using some cabinet catches (https://www.screwfix.com/p/essentials-toggle-cabinet-catches-nickel-plated-45mm-x-36mm-10-pack/15443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).

Thinking the lid could be screwed to the underside or some sort of thick tape to create a seal to the top of the box when locked in place!

RebelDesigner, 2024-08-11:
I was conceptualizing some undermounted drawer, where the bins just slide in. The design would be in a wedged shape, the further you push in the more pressure is applied between some sealing material and the bin. That would lock in place with some mechanism for easy locking/unlocking. This would allow for one handed operation I think. Not a bad thing considering I want to suspend this on a wall eventually.

RebelDesigner, 2024-08-13:
Thanks, can’t wait for the video!
Or maybe a multi part video is also an option? :-P

asucks, 2024-09-09:
I'd still recommend getting a Festool type collection bucket because it will be pressure rated and tested, specifically for this type of use.  I have some of those Ikea Samla containers and they are rather flimsy.  I don't think they'd hold up long term unless your dust extractor wasn't all that powerful.

I found a company selling the 3 pack of Festool bins for $100 shipped on Amazon.  Same company also has them for sale at $90 shipped on eBay and $78 shipped on their website.  They appear to sell overstock Festool items and have good feedback on eBay so it's probably legit.  I should know in a few days.

https://a.co/d/7dxFvvH
https://www.ebay.com/itm/116087171600
https://www.hartvillehardware.com/product/sku-1337339

RebelDesigner, 2024-09-11:
Unfortunately none of those ship to The Netherlands and if they did shipping costs would be significant. Hoping to find a place that sells them this cheap in my area, but I think it will be too expensive for me. I’m going to be stubborn and try some cheaper ones. I got two of these:
https://www.hornbach.nl/p/opbergbox-transparant-grijs-24-liter/10676517/

the dimensions are perfect, the color is pretty cool if you ask me and they are pretty sturdy. I will try to adapt the T-loc design for it and then test how well they hold up. If they are not strong enough I’ll find out.

bartcerneels, 2024-09-11:
> Hoping to find a place that sells them this cheap in my area

I'm sorry. I'm afraid I just bought the last 2 ones from De Vijl (Amsterdam).

I do plan to build multiple of these dust collectors after the initial one based on the current design. At the makerspace the budget is a bit more tight but we have plenty of Ikea SAMLA boxes of various sizes, so very interested in that solution as well.

In fact I have been using a different IKEA product, the [365+10.6L + vacuum seal lid](https://www.ikea.com/be/en/p/ikea-365-food-container-large-rectangular-plastic-10393064/#content) as a container for [a much smaller 3D printed cyclone separato](https://photos.app.goo.gl/8xjP38ZyiMyGPYneA)r. It sort of works but made the mistake of placing the cyclone at the edge instead of the middle and dust gets sucked up again.

asucks, 2024-09-23:
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

I can confirm these are legit Festool and there were 3 of them.

The lids are clear PC, the bins are somewhat yellow and ABS, so I suspect these have just been sitting around for a while and discolored a bit, which is why they are so cheap.

MauiMakes, 2024-09-24:
Thank you so much for creating this and making it available.  I've downloaded all of the files and was going to create a Fusion assembly out of it.  I noticed the fusion EU file assembly but it doesn't contain all parts.  Do you have the full assembly posted anywhere?

Makerr-Studio, 2024-09-25:
Thx a lot! I’m new to Fusion and have the goal to eventually make the whole design native in Fusion. My free time is limited so this is what I got at the moment.

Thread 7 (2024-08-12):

Trouble with the overhangs for the impeller

RebelDesigner, 2024-08-12:
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

Hi,
Printing with PLA on an A1 and the impeller is just really hard to print for me.
Used the Bambu 3mf files and speeds.
This is my second attempt now with lower speeds.
Thinking of printing this also with even lower speeds on the overhangs (now the defaults for slowing down during overhangs).
Did anyone else have such a hard time printing this?

Makerr-Studio, 2024-08-12:
I made a short about that topic;
https://m.youtube.com/shorts/qC6KJh5NBew

I printed the first one in januari when it was colder.
now I need to print with the door open en top cover removed. The normal impeller printed fine on my X1 carbon. It was the mirrored impeller that caused issues.

RebelDesigner, 2024-08-13:
I started to suspect room temperature as well. The printer was in a closed off room all night and the graph of an external temperature sensor is pretty much in line with the ugly overhangs. At a certain point the temperature starts to drop and the overhangs gradually start to look better.

I will wait a few days until the temperature starts to drop here so I hope it results in a better print!
Thanks!

RebelDesigner, 2024-09-05:
I cannot get the impeller to print correctly.
Have tried everything. Printing when the ambient temperature was lower, and even an airconditioned room at 18 degrees.
Slowing down to 50% printing speed on the A1 also does not improve to a perfect result.

Any tips I can try?

RebelDesigner, 2024-09-05:
I have not. It was a new spool straight from the vacuum packaging.

RebelDesigner, 2024-09-09:
I bought a dryer and dried it. Indeed, also with a new spool this time, the result is much better. It’s not perfect yet. The front side is now smooth, yet the back (so the actual overhang) is still a bit of a moon landscape. I think next I’m going to install the prusa slicer and see if I can get a decent quality print of the mirrored impeller. Maybe the slicer also makes a difference.

Btw I printed with overhang speed of 30mm/s. That seems to give the best results.

asucks, 2024-09-09:
What quality settings are you using in Bambu Slicer?  I would recommend switching the print order to "outer/inner" if you haven't already.  This will fix a lot of those issues.

You can also mess around with "Arachne" wall generator settings, as that can usually improve more detailed overhangs/curves in the slicer.

I would continue to slow down as well.

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

Makerr-Studio, 2024-09-09:
Did you try the OrcaSlicer and clockwise printing already?

RebelDesigner, 2024-09-10:
I have been printing other stuff yesterday so I haven’t had time to play with OrcaSlicer yet. I will try tonight.

Thanks for the tips regarding the order of walls. I will also do a test print with that setting later.

RebelDesigner, 2024-09-11:
Tried switching the order of walls as well as the Arachne wall generator. Unfortunately no real improvements.

I have one pretty decent print (slowing down the overhangs to 30mm/s, but slowing down the entire print to 50%) where only the overhanging side of the fins are a bit like sandpaper, but the top side is looking OK. I’m going to sand that back side a bit and call it good. Next up today will be the Orca Slicer for the mirrored impeller.

I think in general this design can only be printed on the really high end machines. An A1 is just not good enough. Not sure if the design can be changed for easier printing without changing its characteristics.

Makerr-Studio, 2024-09-11:
If you still can’t get the impeller smooth I can print them for you. I believe you live in the Netherlands so sipping will not be a problem. Are you making the EU version?

RebelDesigner, 2024-09-11:
That is nice of you to offer! I do live in NL (Breda area), so I might take you up on your offer. Thank you.

I tried the Prusa Slicer with the mirrored impeller and the direction reversed. Had to stop the print after two hours because the quality was really bad again. Looking at the design though, is there a reason for the fins to be about 1mm thick on the bottom while being almost 3mm thick on the top? Making the fins thicker might help with stability while printing?

Makerr-Studio, 2024-09-12:
I did not designed the impellor blades myself. It is a 1:1 copy from the original file from pilson guitars. So a lot of people did print it this way. I only made the mirrored version of it 😅.

RebelDesigner, 2024-09-12:
@Stevenpolak both versions. Up until yesterday I only tried printing the non-mirrored version. Both have problems.

@Makerr-Studio if the offer still stands to print them for me I would like to take you up on that! Let me know what the best way is to get in touch.

Still find it weird that I am having such a hard time printing this. I must be doing something wrong. Or the A1 is just not capable of printing such a difficult part.

Makerr-Studio, 2024-09-12:
Yes it still stand. You can contact me on info@capturingdust.com.

cewalker7, 2024-12-27:
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
I am having the same issue. I have tried various settings   Any settings advice?  I have also tried opening my P1S and putting a box fan pointing in it.

cewalker7, 2024-12-27:
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
I am having the same issue. One side looks better but the overhang part not so much.  I have tried various settings   Any settings advice?  I have also tried opening my P1S and putting a box fan pointing in it.

jmichas, 2025-02-01:
I am adding my settings for my P1S that have been working well so far. I am about 1.5h into my 8h print. Previously I had the same rough issues that others had very early in the print so I aborted.

I started with the posted 3mf and made changes.

So my changes are (using orca slicer):
Wall Order: Outer/inner
Wall Loop Direction: Clockwise

Speed:
First Layer: 30
First Layer Infill: 50
Overhangs:
first box (10%,25%): 30
second box (25%,50%) : 20

Filament Settings for Bambu PLA Matte, which is what I am using:
Nozzle temp: 225/225
Textured PEI Plate 58/58

Cooling:
no cooling for first 3 layers
part cooling fan 100%/100%
Aux fan speed 100%

after first 3 layers are printed and I hear the fans start I also bumped the chamber fan to 90%

So far everything is super smooth, not even a booger anywhere.

Fingers crossed....

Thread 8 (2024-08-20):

tube length

philreindl, 2024-08-20:
I bought the 6"x36" tube listed on the parts list, assuming it would be cut into two parts.  But looking at the plan, am I reading it right that we are to cut that into 500mm long segments?
500mm is 19.7", which of course is more than half of 36"

I have printed the parts for the original mk2 files.

Thanks
Phil

Makerr-Studio, 2024-08-20:
I had the same thoughts on that. I used around the same length that Tim from Pilson Guitars used in his version. Only the offcut is a lot! I did not gamble on it and ordered 2 tubes and kept the same size and rounded it out on mm.

In my tests so far I think you can do with a bit less length and use the 18”. So you only need one tube. Don’t know how much it effects performance.

philreindl, 2024-08-20:
Hrm.  I wonder how much it would matter.  My biggest concern is that the airflow would be significantly reduced using the long-cone as designed.  The long-cone intrudes into the mouth of the outlet by about an inch, which would reduce the open area of the outlet considerably.  Maybe with a shorter long cone it would be fine.

Makerr-Studio, 2024-08-20:
Next week I can adjust the size for you if that would help!

philreindl, 2024-08-20:
Might be worth adding to the experimental files section.  My son has a science fair coming up, maybe this is a worthy experiment he can do for me

Makerr-Studio, 2024-08-24:
@philreindl
I reduced the length by 1.6 inch. Step-file is in the folder:
https://github.com/Makerr-Studio/CentrifugalDustSeparator-/tree/main/MK2/NOT%20TESTED%20-%20REQUESTED%20PARTS

philreindl, 2024-08-28:
awesome, thanks!

Closed 2024-08-28.

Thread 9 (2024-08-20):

Add original CAD files to the repo

poldim, 2024-08-20:
I think you're using Inventor for creating these files.  I'd like to make a few modifications before printing and working with STLs is painful.  Can you create an export for Fusion using the [Pack and Go feature](https://www.autodesk.com/support/technical/article/caas/sfdcarticles/sfdcarticles/How-to-export-Inventor-assembly-files-and-open-them-in-Fusion-360.html)?

Makerr-Studio, 2024-08-21:
Yes Inventor it is for now. I am learning fusion so I can make all the parts native fusion in a way the tube dimensions are easy changeable for someone who has a different tube size.

Next week when I am back home I will make the Pack and Go for you.

phcjpp, 2024-08-23:
That would be great for me also. I also have AD Fusion and a Prusa printer and I can't get either the STL or bamboo files to load in either. I am in the UK btw so really appreciate the UK versions! Thanks so much for doing this.

poo0ooq, 2024-08-23:
Ah, I have the same need as well.

rgodin974, 2024-08-24:
Hello, you did a good job. I'm also interested in Fusion files. Thank you so much.

DBT85, 2024-09-10:
This would also be nice for me.

Makerr-Studio, 2024-09-11:
I am working on the native Fusion Files, this is for the long therm the best solution so you can scale them accordingly.

DBT85, 2024-09-11:
I am wondering how certain things have been drawn, as scaling the impeller is one thing, but I would not want to scale the 3mm o-ring size, even though obviously we would need to scale the diameter of the oring.

Makerr-Studio, 2024-09-12:
That is exactly why we need make the files available in native fusion so people can adjust the tube size accordingly to their own exact tube size without scaling te rest accordingly. I will focus on the in and outlets first so you can use them a.s.a.p!

poldim, 2024-09-12:
> That is exactly why we need make the files available in native fusion so people can adjust the tube size accordingly to their own exact tube size without scaling te rest accordingly. I will focus on the in and outlets first so you can use them a.s.a.p!

yea, for sure!! native fusion files would be best!

btw, there are two ways to share files:
- you can [share](https://help.autodesk.com/view/fusion360/ENU/?guid=ASM-SHARE-DESIGN) them as a link which has the benefit of constantly updating as you make tweaks to them but allow users to download them, this doesn't lend itself to revision control, but has the benefit of always being the latest and greatest version that you've made/tweaked
- you can "[export](https://help.autodesk.com/view/fusion360/ENU/?guid=ASM-EXPORT-DESIGN)" the file from fusion and then drop it in the repo, anytime you have major edits that you'd want to publish, you'd need to re-do the export/upload but that way you have rev control

Makerr-Studio, 2024-09-22:
I am working on the Fusion File for de MK2_EU version of the separator. Today I made the 3D models of the Inlet, Outlet, and Impeller Shroud. So you are able to change the dimensions more easy. I made a Fusion Archive file of the assembly: https://github.com/Makerr-Studio/CentrifugalDustSeparator-/tree/main/MK2_EU/Fusion

Are you able to open it?

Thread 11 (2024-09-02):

Type of extractor

Stevenpolak, 2024-09-02:
Hey, great project! Love to build it / contribute to it. In your videos you use a dual motor camvac, have you been able to test it with others? I, for instance, have the HBM 50 extractor with 1HP 900m3/hr as spec. Will this be enough, or do you really need the pressure from a camvac/shopvac? If you are in/around Amsterdam I could drop by and test it with this extractor.

DBT85, 2024-09-10:
The original Harvey device uses a HVLP blower like your HBM50 and is only rated to 1.5kw for the Gyro 700, so yours should work just fine.

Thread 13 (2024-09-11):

DXF for mounting plate/ french cleats?

voron69-bit, 2024-09-11:
Any chance you'd be willing to share those files as well? Even if you don't have a CNC, they are useful for layouts to make by hand.

Thank You! I can't wait to see your next videos!

Makerr-Studio, 2024-09-11:
In the folder [MK2_EU](https://github.com/Makerr-Studio/CentrifugalDustSeparator-/tree/main/MK2_EU) I added the Shaper files (and also the DXF's) and the Fusion files of the baseplate and cleat.

Closed 2024-09-11.

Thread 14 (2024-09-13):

US - Parts Deals - and typo in README.md

ver2go, 2024-09-13:
Not an issue, but wanted to share deals I found for parts. Please delete if not appropriate, or if there is a suggestion for a better place to post.

US only

Clear PVC 6"
https://www.woodcraft.com/products/woodriver-dust-connection-clear-pvc-tube-36-x-6
Free Shipping with Code "PENCIL" $20 each
* note, scale to 99.6% seems to work for me. The scale ring indicated 100%.
** note number 2, the scale ring doesn't need walls so thick. I did a quick hack in Freecad and it cut the print time in half. Not sure if that's why it showed 100%, but I only cut out the ID of the scale ring

Festool Storage VAB-20/3
$79.60 set of 3 - Free shipping
https://www.hartvillehardware.com/product/sku-1337339/festool-dust-extractors-accessories

An Issue (typo)
https://github.com/Makerr-Studio/CentrifugalDustSeparator-/blob/main/README.md?plain=1#L48-L49
jet = yet?

voron69-bit, 2024-09-14:
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

Not sure what you're talking about the scale ring, but I've already got all my parts printed, and O rings installed. Does this 6" pvc work or not? I'm not reprinting or buying new orings.

asucks, 2024-09-23:
> Does this 6" pvc work or not? I'm not reprinting or buying new orings.

These clearance 6" PVC tubes are the same as the original 6" PVC tubes linked.  I got the clearance ones this morning and they are identical.

voron69-bit, 2024-09-23:
> > Does this 6" pvc work or not? I'm not reprinting or buying new orings.
>
> These clearance 6" PVC tubes are the same as the original 6" PVC tubes linked. I got the clearance ones this morning and they are identical.

They are not. I too bought the clearance ones, and you have to reduce all the parts to 99.2%

ver2go, 2024-09-23:
> > Does this 6" pvc work or not? I'm not reprinting or buying new orings.
>
> These clearance 6" PVC tubes are the same as the original 6" PVC tubes linked. I got the clearance ones this morning and they are identical.
 I thought they were where I looked at the specs compared to the powertec ones. I figured they were both imported/own from the same company.

I didn't have an original powertec one to confirm.

Did you have to scale yours? 99.6% for for me. 100% didn't on my first inletnprint test.

asucks, 2024-09-23:
> They are not. I too bought the clearance ones, and you have to reduce all the parts to 99.2%

Maybe they are on clearance because of slight manufacturing differences?  Or maybe they are poorly cut and the edges just need to be deburred?

> Did you have to scale yours? 99.6% for for me.

What material did you print with?

Can you guys measure the inside ID with calipers?  I have several of them so I can take some measurements soon.

voron69-bit, 2024-09-23:
Yeah probably a manufacturer issue, since they are clearance. I print in ABS, and my printer is good out to 0.05 XYZ accuracy. So I know its not my prints. ID of this clearance tube is anywhere from 145.27 to 145.59. I could have gone SLIGHTLY larger than 99.2, but 99.3% was too snug and 99.2% fit just fine. I wasn't about to get in the weeds over a fraction of a percent.

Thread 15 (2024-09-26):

Différence entre MK2 et MK2 EU

BILLYJOYCE, 2024-09-26:
Bonjour, c'est la différence entre les deux versions ? merci

Makerr-Studio, 2024-09-26:
Hello! The MK2 are designed for the 6" Powertec pipes you can buy in USA on Amazon.

When you live in Europe and have the Acrylic tubes from kunststofforte.nl you need the MK2_EU.

There are scaling rings available for the different version to finetune the measurements because of production tolerances.

You need to order the tubes first and than select the right files for it accordingly. See the readme files at each version.

Hope this info helps!

BILLYJOYCE, 2024-09-26:
Merci beaucoup pour toutes ces explications, c'est parfait. 👌👍

BILLYJOYCE, 2024-10-21:
Malheureusement, après trois essais avec mon imprimante x1c, le fichier 3mf n'est pas forcément compatible. Elle a du mal à gérer les surplombs.
Il faut trouver le bon réglage, ce qui n'est pas simple au niveau du surplomb des pales.

BILLYJOYCE, 2024-10-21:
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

Makerr-Studio, 2024-10-21:
J'ai pu très bien imprimer la turbine ordinaire avec mon x1c. J'ai imprimé la turbine en miroir dans le sens des aiguilles d'une montre avec l'Orhca Slicer et j'ai ouvert la porte et la plaque supérieure pour maintenir la température plus basse. J'ai imprimé avec du bambou lab mat pla.

BILLYJOYCE, 2024-10-22:
Je fais comme vous en règle générale avec le PLA Sinon c'est pas terrible, mais là le surplomb me donne du fil à retordre.

BILLYJOYCE, 2024-10-24:
Bonjour, c'est à dire en miroir ?

Makerr-Studio, 2024-10-25:
Je pense que votre buse doit être remplacée à en juger par la qualité d'impression

patrickstolc, 2025-03-10:
For the EU version the reference build uses acrylic, but would polycarbonate work as well? I've noticed [it's available](https://www.kus-kunststofftechnik.de/polycarbonat-rohr-o-150-mm-laenge-waehlbar-von-100-bis-1400-mm/) in large diameter and even cut to size.

Is there any reason why PC wouldn't work? I have very little experience with PC and acrylic, but PC doesn't have the same tendency to crack as acrylic.

Makerr-Studio, 2025-03-10:
Polycarbonate offers much more resilience than acrylic. Acrylic is more transparent, while polycarbonate is easier to scratch.

I chose Acrylic because I could buy that the easiest.

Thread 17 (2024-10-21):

Add to your concept

mspianos, 2024-10-21:
Hello,

I don't know where to contact you so I put my message here, I will remove it if it is not in the right place.

I thought last night, I know I should sleep, to add the engine, the filter and a third tank directly in your design. It is just a schematic.

Do you think that the idea is to be further explored, or should I go to sleep?
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

Makerr-Studio, 2024-10-21:
Sleep is good but I like your way of thinking!

I doubt whether such a third phase is efficient. I think the tube diameter needs to be smaller to achieve the higher speeds and separate the very fine particles.

I'm looking into a slightly different option to place a NanoMax style cartridge filter + motor on the side of the second bin (not in line). I don't have the space above my planer for the available length. And I try to make more use of gravity in the last filter so that the fine particles spin arount the filter and fall down the side of the motor so that it can be easily emptied.

We discuss this kind of thing more on my Patreon. And we've set up a Discort server for ideas like this you can join

mspianos, 2024-10-21:
I don't know Patreon, it seems to be paid, right?
For Discord, do you have a link to your server to give me?

Makerr-Studio, 2024-10-21:
Yes Patreon is a way to support me and you get my support and that from the community back. I will update on my progress and share exclusive test files to print yourself. When you become a tier member the Discord server is automatically released for you.

Github is the free option to contribute! Only I check that twice a week. Patreon I watch and react on a daily basis.

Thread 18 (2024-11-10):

Please add Full CAD Files for the EU Version

Leo-Wolf-the-Engineer, 2024-11-10:
Hi,

could you add the CAD files (STEP or Fusion) of the complete assembly for the EU Version?
I need those for further planning.

Thank you
Leo

Makerr-Studio, 2024-11-27:
You can download the complete STEP-file on my Patreon. It's a free product for all my supporters.

https://www.patreon.com/CapturingDust/shop/complete-step-file-mk2-eu-720835

Closed 2024-11-27.

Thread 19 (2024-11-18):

Anyone built an Australian version?

ctolkien, 2024-11-18:
As per title. Acrylic tubes are expensive!

IanVicAus, 2024-12-25:
FYI the link is for 1m of 145mm ID acrylic tube (2.5mm wall thickness) @ $133 / m (enough for 2 tubes @ 500mm)
Obviously this needs a different set of sized pieces (and first the ID accurately measured)
Price wise the same as importing tube from Amazon (which is PVC not acrylic, it is also thinner ~2mm v 2.5mm).
No association tot he website
https://www.acrylicsonline.com.au/products/extruded-clear-acrylic-tube-150mm

ctolkien, 2025-01-05:
Yep, that's the one I've been looking at - I think someone will have to pull the trigger on ordering this and figuring at the sizes.

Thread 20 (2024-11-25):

Tube sourcing links

3dtrix, 2024-11-25:
Hi,

in Germany i buy my tubes from this online shop:

Original Plexiglas manufacture:
150mm / 3mm
https://www.plexiglas-shop.com/de/produkte/ro0a070gt.html

They ship to EU incl. UK

cheers
Carsten

Makerr-Studio, 2024-11-27:
Thx for sharing! I added it to the EU and UK build versions.

Makerr-Studio, 2024-11-27:
Thx for sharing! I added it to the EU and UK build versions.

Closed 2024-11-27.

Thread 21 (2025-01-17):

Orca Slicer impeller mirror 3mf file not opening

Crzy88, 2025-01-17:
Im getting an error when trying to open the impeller mirror 3mf file. Whilst my Bambulab studio is up to date it says that the file requires a newer version.

Any suggestions on this?

The regular impeller mirror file in the bambulab folder opened normally. Whilst printing I did encounter the issues described in the video. Triggering me to look in the orca slicer folder.
Is there even a difference or should I adjust  some settings?

thnx in advance!

ErikCrombag, 2025-01-17:
3mf files saved in Orca don't open in Bambulab Studio. (At least not on my pc and judging from your comment, not on yours)
You should download and install Orca Slicer for this. [Stable version on Github](https://github.com/SoftFever/OrcaSlicer/releases/tag/v2.2.0)

Opening the mirror impeller in Orca and printing it from there worked fine for me. (Bambulab A1 printer)

Makerr-Studio, 2025-01-17:
Erik described it perfectly. The orca slicer supports counterclockwise printing. It is based on the Bambulab slicer.

The normal impeller should print fine through. It’s only the mirrored impeller that courses issues for me.

Crzy88, 2025-01-17:
Thnx all, new to it all so this helps. Will checkout the orca slicer.
The normal impeller is printed correctly indeed.

Crzy88, 2025-01-19:
Having some trouble setting up the orca slicer, does not seem to link with the printer. Don't know if they already executed the security update that was announced this week?
Have one turbine now assembled.

Why do we need the mirrored impeller ? Can't I use 2 normal ones?

Makerr-Studio, 2025-01-19:
They already punched the update! Really disappointed in Bambu Lab.

You don’t need the mirrored impeller. It’s just for the looks. Only pay attention to the dust outlet port of the second stage. It needs to be the same as the other impeller.

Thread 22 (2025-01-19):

Tips for the yet to be made Fusion files

jmichas, 2025-01-19:
Well, this is sort of a tip and sort of my opinion.

First, thanks so much for releasing all this, it is really amazing and I can't wait to make mine.

When you create the fusion file(s) instead of just releasing them so people can update them for their specific use case/material availability, I think you should make them parametric.

In looking at all the files you have posted, it appears that only a small set are needed to change for tube type. So, pick out all the parts that are tied to ID, OD and wall thickness of the pipe and make those values parametric. Then people can use the fusion files to easily generate new step/stl files when they measure their actual pipe. Simply punch in new values for those 3 variables and the models will change instantly.

This would be better than simply scaling a part because scaling will affect things you want to remain standard across all pipe sizes like the inlet outlet where it attaches to hoses and fittings or o-ring channel dimensions.

If you would like help with parameterizing the fusion files let me know.

Thanks again for all your great work.

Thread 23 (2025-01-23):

Scaling Ring

jmichas, 2025-01-23:
How tight should the scaling ring be? I can jam it on until about 100.35% but it is snug at closer to 100%
I am using a pipe from amazon US that is polycarbonate, it seems like it will work fine.

What part would be the first to print as a test part? Inlet/Outlet?
And is the MK2 design o-ring still 140mmx3mm? Or is it 120x3 now too?

Thanks

Makerr-Studio, 2025-01-24:
I would go for 100% in your case. Just snug is good enough. Jamming it on is often to tight. For MK2 you need 140x3. The tubes for MK2_EU is a bit smaller in diameter so 120x3 in that case. I would probably go for the inlet for your first real print. Enjoy the build!

jmichas, 2025-01-29:
Ok, I wanted to wait until I had an actual printed part (the inlet) and o-rings to make sure the ft was good before I reported on what I am using.
I got this polycarbonate tube off amazon https://www.amazon.com/dp/B0C4PM29X1?ref=ppx_yo2ov_dt_b_fed_asin_title&th=1
and I printed it at 100.1% and it worked fine, it may also be fine at 100% but based on the scaling ring I felt the pipe was a whisper bigger than 100%.
I know I could have just bought the PVC pipe but, for roughly the same price I wanted the clear look because it looks cooler.

jmichas, 2025-01-29:
Oh, and now, printathon 2025 begins!

Closed 2025-01-29.

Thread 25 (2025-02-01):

Printing Tips Bambu P1S/X1C

jmichas, 2025-02-01:
Mostly my printing has been going flawlessly.

I also added a stacked version of the brackets so all 8 can be printed at the same time as long as you have an AMS and some PETG (PR pending). It takes 6 hours but you can run it overnight.

My problem has been with the Y inlet/outlet brackets. I had 4 failures in a row where the part warped on the end and got bumped by the nozzle, then it was a rats nest of filament everywhere.

What eventually worked for me was turning off the aux fan, setting the parts fan to 50% and no cooling for the first 3 layers.
It is similar to what I do with large gridfinity bins and I print those with no brim.

Hopefully this helps someone.

Also, maybe we need a wiki area for troubleshooting stuff like this etc.

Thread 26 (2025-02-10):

Cutting jig?

Crzy88, 2025-02-10:
Hi all,

I'm almost at the point where I can perform a test run. All is printed. Made a housing to hold my 2x 60+ltr dust bins based on eurobox and custom clamps.
The pipes have been assembled but I still need to cut the holes for the actual dust to go through.

Is there a cutting jig available  by any chance?

small preview:

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

Makerr-Studio, 2025-02-10:
There are no cutting jigs for the baseplate. You can print the fist few layers of the dust outlet ports  and use them to mark the holes more easily. Hope this works out for you!

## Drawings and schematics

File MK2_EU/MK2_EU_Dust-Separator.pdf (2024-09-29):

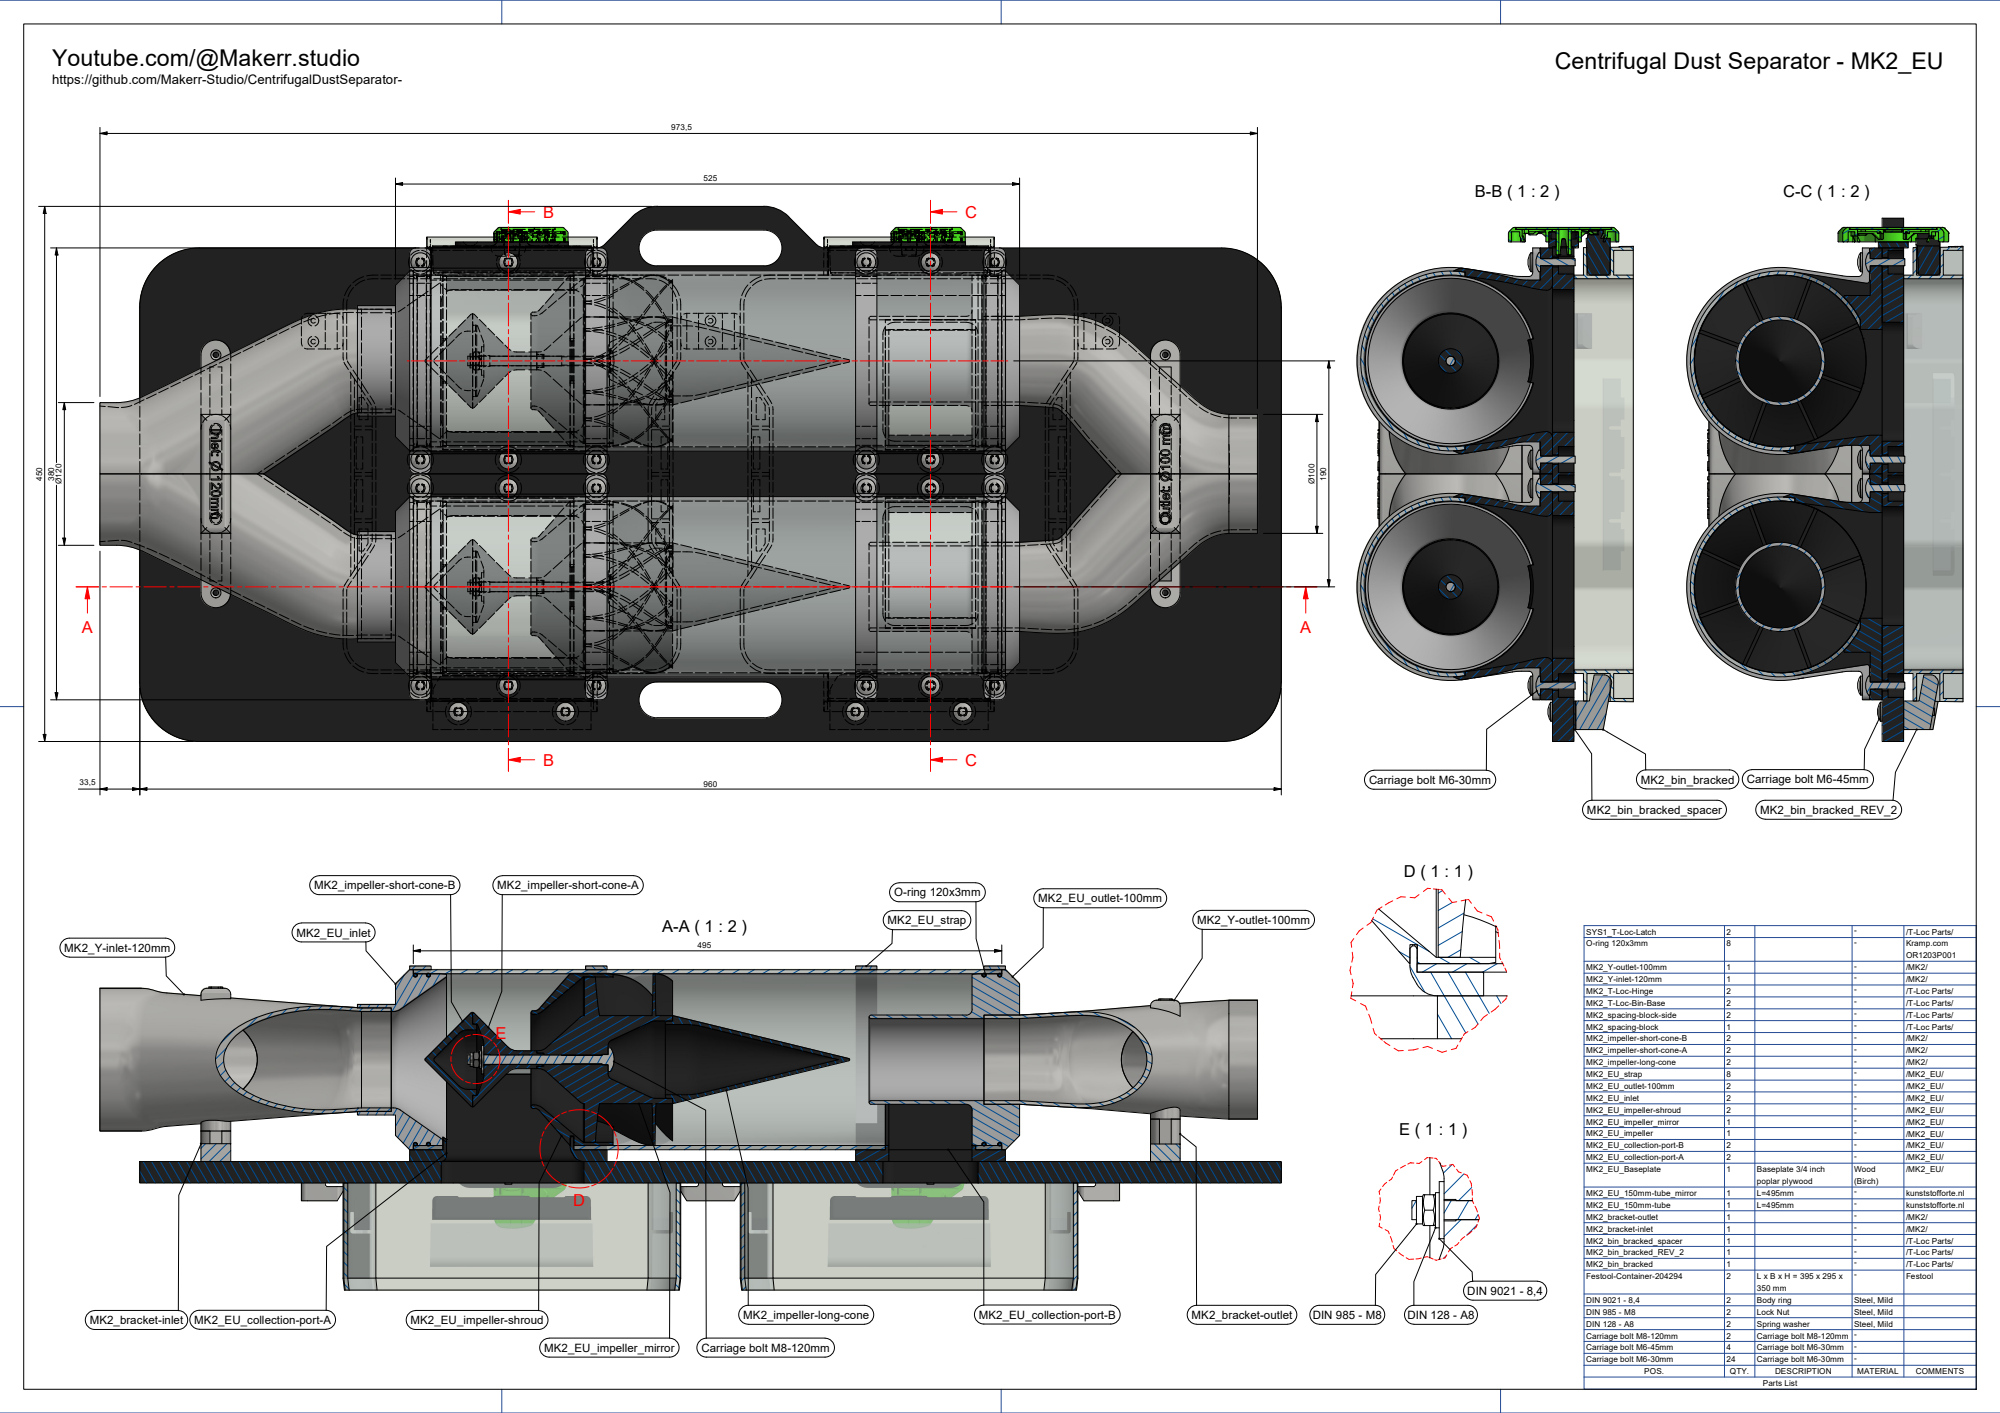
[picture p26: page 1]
/T-Loc Parts/ SYS1_T; - -Loc-Latch; - -ring 120x3mm; - -outlet-100mm; - -inlet-120mm; /T-Loc Parts/ MK2_T; - -Loc-Hinge; - -Loc-Bin-Base; /T-Loc Parts/ MK2_spac; - ing-block-side; - ing-block; - impeller-short-cone-B; - impeller-short-cone-A; - impeller-long-cone; - trap; - tlet-100mm; - inlet; - impeller-shroud; - impeller_mirror; - impeller; - llection-port-B; - llection-port-A; Baseplate 3/4 inch; poplar plywood; kunststofforte.nl MK2_EU_150mm; - -tube_mirror; - -tube; - racket-outlet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

Youtube.com/@Makerr.studio

Centrifugal Dust Separator - MK2_EU

https://github.com/Makerr-Studio/CentrifugalDustSeparator-

MK2_EU_collection-port-B MK2_bracket-inlet MK2_EU_collection-port-A

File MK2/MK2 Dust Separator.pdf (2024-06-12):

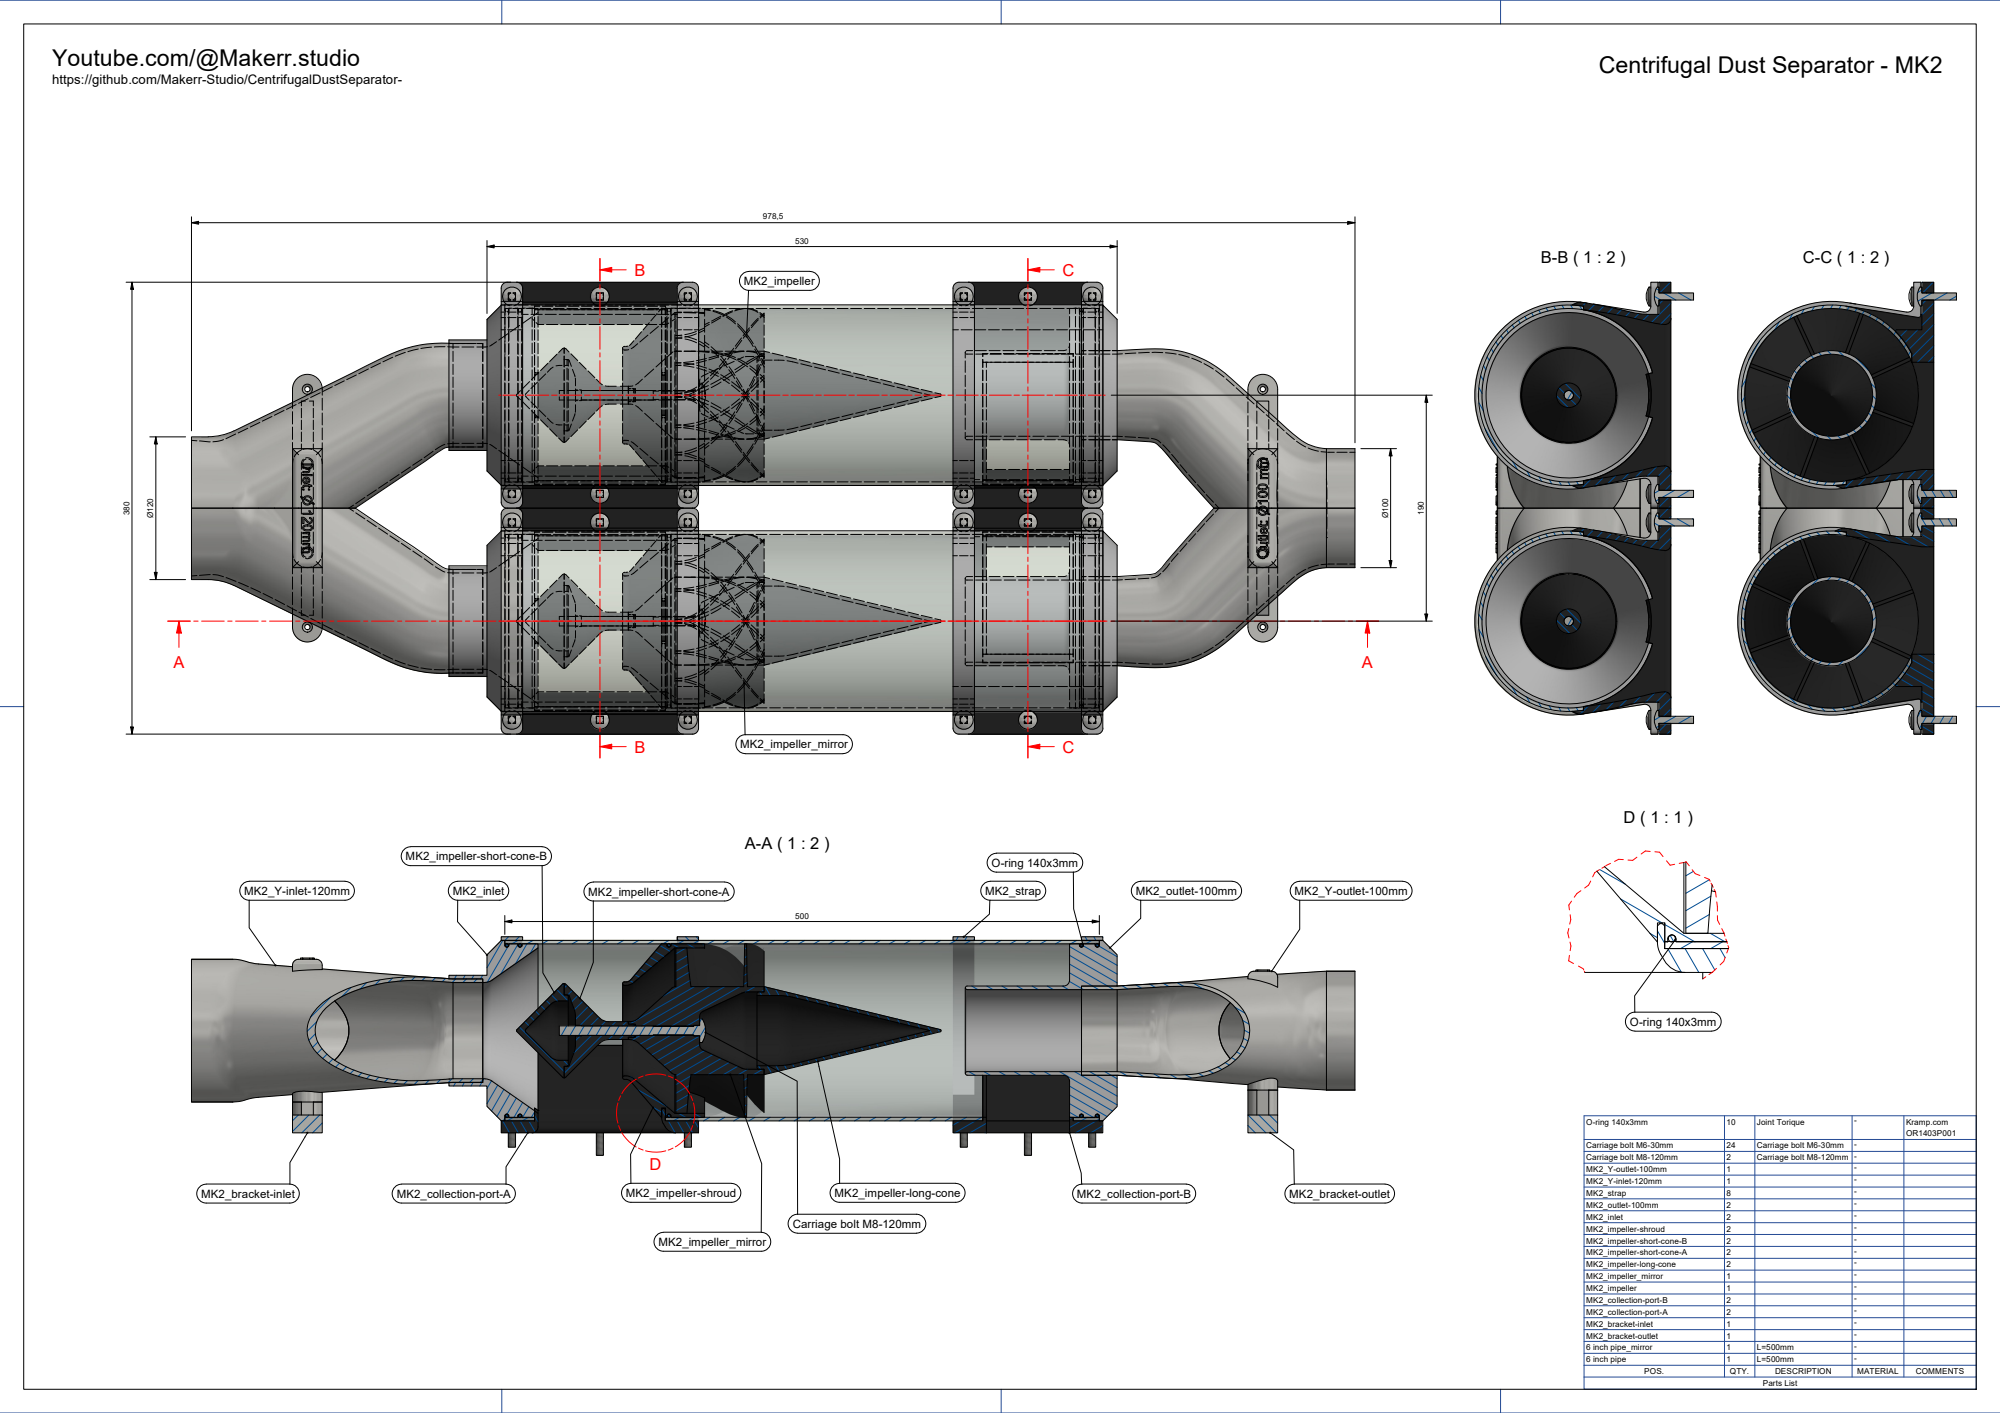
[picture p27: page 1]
- O-ring 140x3mm; int Torique; - Carriage bolt M6-30mm; rriage bolt M6-30mm; - Carriage bolt M8-120mm; rriage bolt M8-120mm; - -outlet-100mm; - -inlet-120mm; - trap; - tlet-100mm; - inlet; - impeller-shroud; - impeller-short-cone-B; - impeller-short-cone-A; - impeller-long-cone; - impeller_mirror; - impeller; - llection-port-B; - llection-port-A; - racket-inlet; - racket-outlet; - inch pipe_mirror; - inch pipe; Parts List; Carriage bolt M8-120mm; O-ring 140x3mm

Youtube.com/@Makerr.studio

Centrifugal Dust Separator - MK2

https://github.com/Makerr-Studio/CentrifugalDustSeparator-

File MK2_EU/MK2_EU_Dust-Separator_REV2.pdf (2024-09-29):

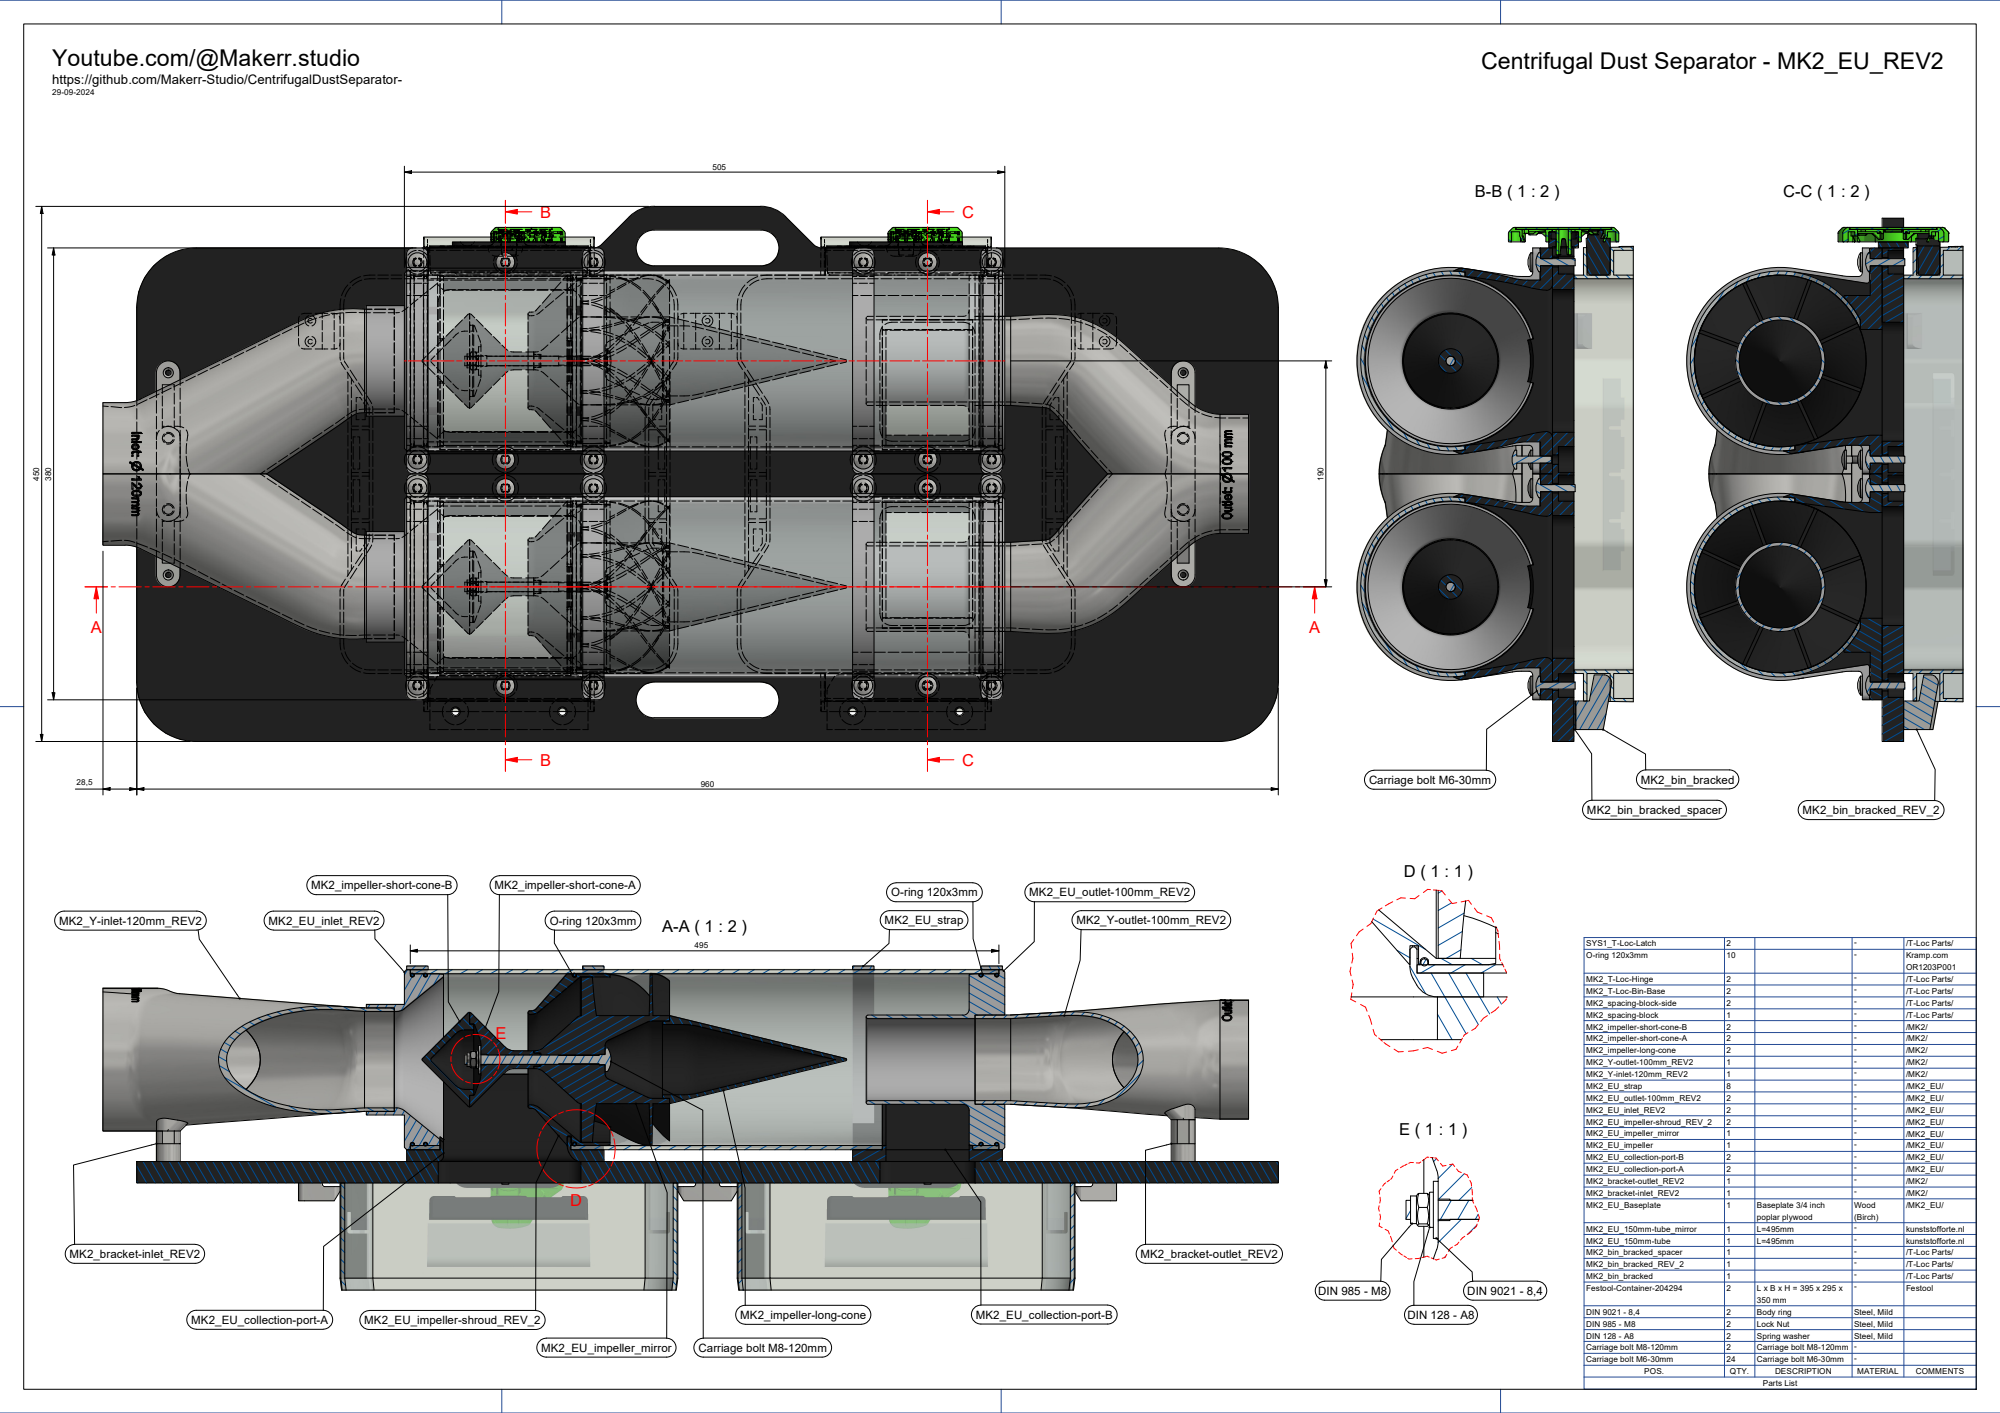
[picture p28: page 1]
/T-Loc Parts/ SYS1_T; - -Loc-Latch; - -ring 120x3mm; /T-Loc Parts/ MK2_T; - -Loc-Hinge; - -Loc-Bin-Base; /T-Loc Parts/ MK2_spac; - ing-block-side; - ing-block; - impeller-short-cone-B; - impeller-short-cone-A; - impeller-long-cone; - -outlet-100mm_REV2; - -inlet-120mm_REV2; - trap; - tlet-100mm_REV2; - inlet_REV2; - impeller-shroud_REV_2; - impeller_mirror; - impeller; - llection-port-B; - llection-port-A; - racket-outlet_REV2; - racket-inlet_REV2; Baseplate 3/4 inch; poplar plywood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

Youtube.com/@Makerr.studio

Centrifugal Dust Separator - MK2_EU_REV2

https://github.com/Makerr-Studio/CentrifugalDustSeparator-

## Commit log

2024-07-10 Delete MK2/STEP/MK2_inlet.stp
    Chamfer 0.2 to shallow. Needs to be 0.5.
    [MK2_inlet.stp]
2024-07-10 Delete MK2/STEP/MK2_outlet-100mm.stp
    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
    [MK2_outlet-100mm.stp]
2024-07-10 Add files via upload
    Chamfer 0.2 was to shallow. Adjusted to 0.5 for easier assembly in Pipe.
    [MK2_inlet.stp, MK2_outlet-100mm.stp]
2024-07-20 Add files via upload
    Bracket for inlet 125mm is the same as 120mm inlet.
    [MK2_Y-inlet-125mm.stp, MK2_Y-outlet-125mm.stp, MK2_bracket-outlet 125mm.stp]
2024-07-21 Add files via upload
    Add the .3mf files for Bambu Lab and fixed the Non-manifold edges error.
    [MK2_impeller-mirror.3mf, MK2_impeller.3mf]
2024-09-05 Delete MK2_EU/STEP/MK2_EU-spacing-block-side.stp
    Moved the files to the main folder "T-loc Parts".
    [MK2_EU-spacing-block-side.stp]
2024-09-05 Delete MK2_EU/STEP/MK2_EU-spacing-block.stp
    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
    [MK2_EU-spacing-block.stp]
2024-09-05 Delete MK2_EU/STEP/MK2_EU_T-Loc-Bin-Base.stp
    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
    [MK2_EU_T-Loc-Bin-Base.stp]
2024-09-05 Delete MK2_EU/STEP/MK2_EU_T-Loc-Hinge.stp
    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
    [MK2_EU_T-Loc-Hinge.stp]
2024-09-05 Delete MK2_EU/STEP/MK2_EU_bin_bracked.stp
    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
    [MK2_EU_bin_bracked.stp]
2025-01-31 Added a 3mf with 8 stacked straps so they can be printed at the same time
    [MK2_strap_stacked.3mf]
2025-08-16 Add files via upload
    200mm single tube centrifugal dust separator incl. third stage integration.
    [100mm PVC tube.stp, 6 inch pipe short.stp, Baseplate-bracked.stp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]
